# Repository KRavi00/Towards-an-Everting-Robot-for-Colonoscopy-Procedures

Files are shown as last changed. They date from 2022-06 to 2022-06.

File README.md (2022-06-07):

# Towards-an-Everting-Robot-for-Colonoscopy-Procedures
This repository contains all the relevant code and files for the associated Master's project.

The following is included in this repository:
- DC motor control code (for use with an L293D module)
  - Allows robot growth speed and direction control. It is a modified version of the Pre-formed Vine Robot control code [found here](https://www.vinerobots.org/build-one/pre-formed-vine-robot/).

- Pressure sensor conversion code (for use with the SMC PSE543A-R06 sensor)
  - Converts analogue output of sensor into kPa pressure readings.

- CAD files of 3D printed parts used
  - The motor mount and spool are also modified versions of the part files [found here](https://www.vinerobots.org/build-one/pre-formed-vine-robot/).
  - The prototype assembly used to create the renders from the report are also included.

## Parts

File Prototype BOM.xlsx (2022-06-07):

Quantity | Part | Purpose | Link
1 | Plastic Pressure Chamber | Main base and pressurisation chamber for the robot | Lock & Lock LLS143 Round 1.9ltr Container, 1.9 L : Amazon.co.uk: Home & Kitchen (https://www.amazon.co.uk/Lock-Round-Storage-Container-Clear/dp/B00CE0D07E)
1 | LDPE Sheet Roll | Everting Body | Amazon (120 guage/30 microns thickness) (https://www.amazon.co.uk/Light-Clear-Polythene-Layflat-Tubing/dp/B01NCDSI1R)
1 | Low stretch flexible rope | Tie robot body to the spool
1 | Push-to-connect tube fitting | Inlet for air from compressor
1 | Spider coupler | Couple the motor and the spool | https://www.amazon.co.uk/sourcing-map-L26xD20-Flexible-Coupling/dp/B08NJ274QF
1 | Motor | To rotate the spool | https://uk.rs-online.com/web/p/dc-motors/9211445
1 | Stainless steel shaft | Main spool shaft | https://www.amazon.co.uk/KUIDAMOS-Stainless-D%E2%80%91Shaft-Steering-Gobilda/dp/B08SR3B1GX
1 | Arduino Uno | Main board for control | https://www.ebay.co.uk/itm/322898299808?hash=item4b2e3d0ba0:g:bmcAAOSwK~RaFdI3
1 | USB 2.0 Cable Type A/B | Connect board to computer | https://uk.rs-online.com/web/p/usb-cables/1828864

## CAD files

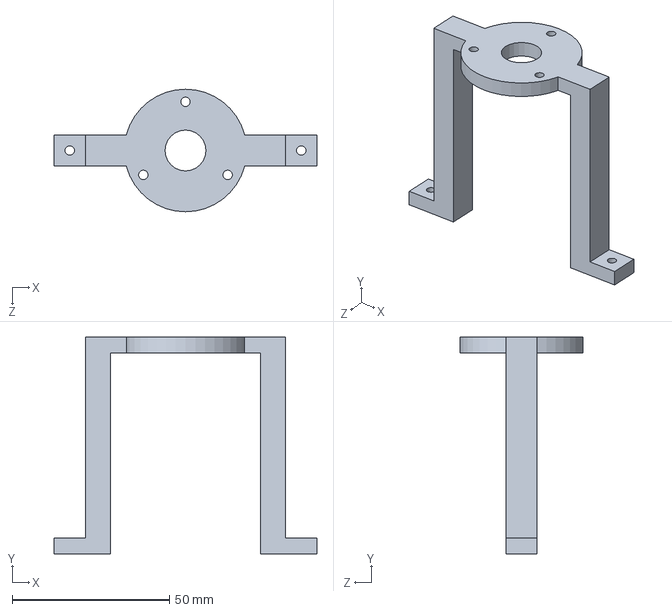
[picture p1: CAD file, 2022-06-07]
3D printed Parts/Motor Clamp v2.SLDPRT
83.7 x 69.0 x 39.0 mm

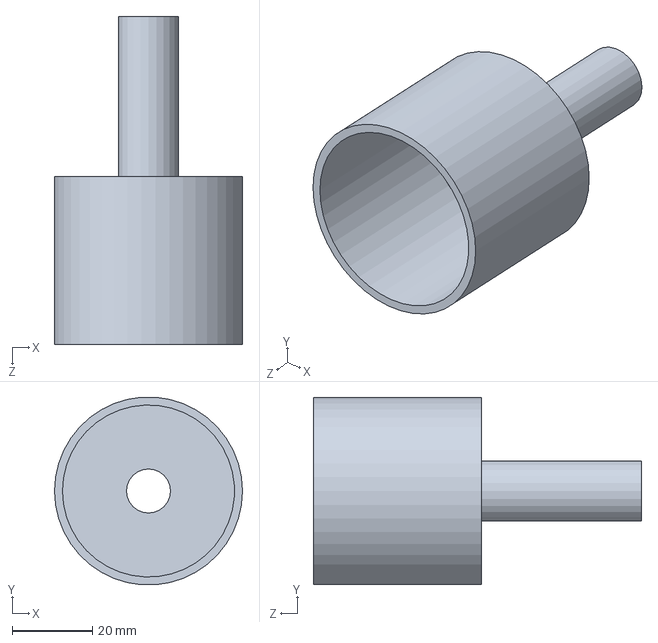
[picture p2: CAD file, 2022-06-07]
3D printed Parts/Outlet Tube 15.SLDPRT
47.0 x 46.9 x 82.0 mm

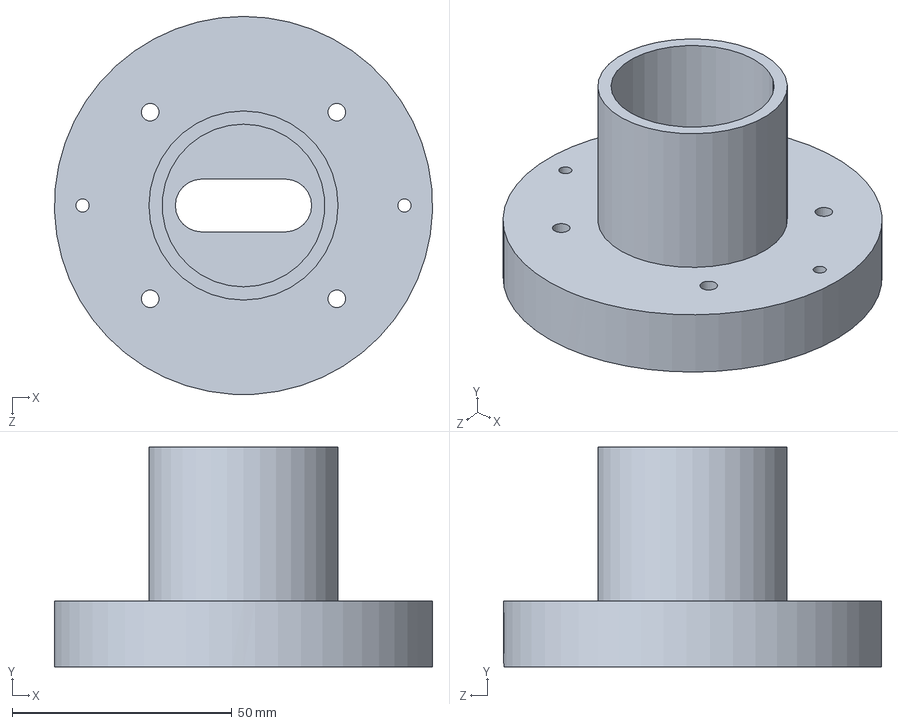
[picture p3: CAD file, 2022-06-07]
3D printed Parts/Motor Base v2.SLDPRT
86.0 x 50.0 x 86.0 mm

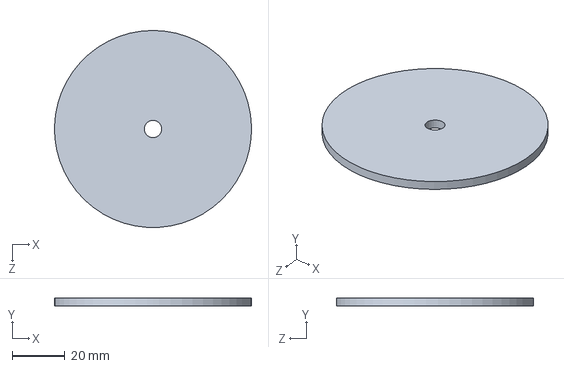
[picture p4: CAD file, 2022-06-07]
3D printed Parts/Spool-End-Modified.SLDPRT
75.0 x 3.00 x 75.0 mm

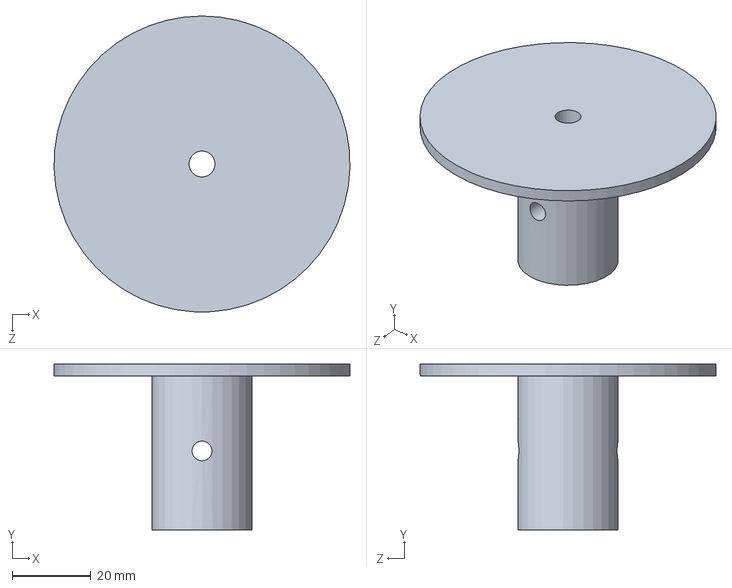
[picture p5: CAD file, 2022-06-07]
3D printed Parts/Spool-Modified.SLDPRT
75.0 x 42.0 x 75.0 mm

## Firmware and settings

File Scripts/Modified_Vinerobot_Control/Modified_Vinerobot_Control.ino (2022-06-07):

/*----------------------------------------------------------
 * This is a modified version of the Vinerobot code provided 
 * on the vinerobot website.
 * This code has been adapted to allow motor control with an
 * L293D module.
 * 
 * Original authors: May 24, 2018, Javier A. Reyna Zepeda
 * Editor: Kiran Ravi, 31/01/22
 */



/*---------------Includes-----------------------------------*/
#include <math.h>
#include <ctype.h>

/*---------------Module Defines-----------------------------*/
#define OFF               0
#define FORWARD           HIGH
#define REVERSE           LOW
#define GROWTH            HIGH
#define RETRACT           LOW

/*---------------Pin Declares-------------------------------*/
int motorPin1    = 9;  // First PWM output pin, connects to negative of the motor
int motorPin2    = 10; // Second PWM output pin, connects to the positive of the motor 
int motorSpeedPin = 11;  // Speed output pin for motor

/*---------------Motor Dependent Parameters-----------------*/
int minGrowthSpeed  = 0; // Minimum speed required to allow growth
int minGrowthStop   = 0; // Minimum speed required to stop growth
int minRetractSpeed = 0; // Minimum speed required to start retraction

/*---------------Control Variables--------------------------*/
int motorSpeed   = 0;      // Controls the motor's speed from 0-255
int speedDelta   = 5;      // Controls the change in speed

bool vineState  = GROWTH; // Is the motor growing or retracting?
 
unsigned char theKey = ' ';

/*---------------Module Function Prototypes--------------*/
unsigned char TestForKey(void);
void RespToKey(void);
void grow(int);
void retract(int);
void halt();
void deflate();
void inflate();

/*---------------Pre-formed Vine Robot Setup ----------------------*/
void setup() {                 // setup() function required for Arduino
  Serial.begin(9600);

  // Output pins
  pinMode(motorPin1, OUTPUT);     // PWM pin for motor -
  pinMode(motorPin2, OUTPUT);     // PWM pin for motor +
  pinMode(motorSpeedPin, OUTPUT);  // Speed pin for motor 1

  // Initialize motor
  analogWrite(motorSpeedPin, OFF);            // set to not be spinning (0/255)
  digitalWrite(motorPin1, HIGH);              // set motor direction to anti-clockwise by setting negative high
  digitalWrite(motorPin2, LOW);               //... and positive low
}

/*---------------Pre-formed Vine Robot Main Loop-------------------*/
void loop() {        // loop() function required for Arduino
  theKey = Serial.read();
   
  
  if (theKey == 'W'){               //GROW, MOVE FORWARD  
    motorSpeed = minGrowthSpeed;
    grow(motorSpeed);
    vineState = GROWTH;
     Serial.println("Growing");
  }

  if (theKey == 'S'){               //RETRACT, MOVE BACK  
    motorSpeed = minRetractSpeed;
    retract(motorSpeed);
    vineState = RETRACT;
     Serial.println("Retracting");
  }

   if (theKey == 'D'){               //INCREASE SPEED      
    motorSpeed += speedDelta;
    speedChange(motorSpeed);         // Input speed change into new speedChange function
    Serial.println(motorSpeed);
  }
  
  if (theKey == 'A'){               //DECREASE SPEED     
    motorSpeed -= speedDelta;
    speedChange(motorSpeed);        // Input speed change to new speedChange function
    Serial.println(motorSpeed);
  }

  if (theKey == ' '){               //STOP              
    halt();
    Serial.println("Stopping");
  }

    if (theKey == 'X'){               //FULL SPEED AHEAD GROWTH
    motorSpeed = 255;
    grow(motorSpeed);
    vineState = GROWTH;
    Serial.println(motorSpeed);
  }

    if (theKey == 'C'){               //FULL SPEED AHEAD RETRACTION
    motorSpeed = 255;
    retract(motorSpeed);
    vineState = RETRACT;
    Serial.println(motorSpeed);
  }
}



/*----------------------Module Functions--------------------------*/
unsigned char TestForKey(void) {
  unsigned char KeyEventOccurred;
  
  KeyEventOccurred = Serial.available();
  return KeyEventOccurred;
}

// Tells the vine robot to grow at a particular motor speed
void grow(int motorSpeed){
    analogWrite(motorSpeedPin,motorSpeed); 
    digitalWrite(motorPin1, HIGH); 
    digitalWrite(motorPin2, LOW);
}

// Tells the vine robot to retract at a particular motor speed
void retract(int motorSpeed){
    analogWrite(motorSpeedPin,motorSpeed); 
    digitalWrite(motorPin1, LOW); 
    digitalWrite(motorPin2, HIGH);
}

// Tells the motor what speed to go at
void speedChange(int motorSpeed){
  if(motorSpeed > 255){
    Serial.println("Already at max speed");
  }
  
  else if(motorSpeed < 0){
    Serial.println("Already at min speed");
  }
  else{  
  analogWrite(motorSpeedPin,motorSpeed);
  }
}

// Stops the vine robot's growth and remains pressurized
void halt(){
    analogWrite(motorSpeedPin,minGrowthStop); 
}

// Pressurizes the chamber
void deflate(){
}

// Deflates the vine robot
void inflate(){
}

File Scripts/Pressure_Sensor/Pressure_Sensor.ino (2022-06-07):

void setup() {
  // put your setup code here, to run once:
  pinMode(A0, INPUT);
  Serial.begin(9600);
}

void loop() {
  // put your main code here, to run repeatedly:
  // -1 bar to 1 bar
  // 0 to 1023 
  
  // output 1v to 5v;
  // starting value 1023/5 = 205// -1bar
  //3v zero pressure 614;
  // 0-101kpa 2v range;
  //(value - 614)/(101kpa - 0)*2 =
  double value = (analogRead(A0));
//  Serial.println(value);
  double cal = 1.17;
  double pres = (value - ((1023.0/5)*3));
  double pres_converted = pres*(250.0/1023) + cal;
  Serial.print(pres_converted);
  Serial.print("\n");
}

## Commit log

2022-06-07 Update README.md
    Added details in readme about full assembly
2022-06-07 Add files via upload
    Added all scripts and CAD files to the repository
    [Motor Base v2.SLDPRT, Motor Clamp v2.SLDPRT, Outlet Tube 15.SLDPRT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]
2022-06-07 BOM upload
    Uploaded prototype BOM
    [Prototype BOM.xlsx]
